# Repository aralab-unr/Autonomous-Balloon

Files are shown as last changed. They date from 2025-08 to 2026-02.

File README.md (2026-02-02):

<div align="center">
    <h2>Autonomous Balloon: Autonomous Balloon based Adaptive Sliding Mode Control and Infinite-Horizon POMDP</h2>
</div>

# Highlights
Our paper has been accepted for publication in ICRA 2026. If our repository supports your academic projects, please cite our work. Thank you!
[Balloon_POMDP_ASMC_ICRA.pdf](https://github.com/user-attachments/files/25022309/Balloon_POMDP_ASMC_ICRA.pdf)

This project provides a simulation platform for super-pressure balloons, featuring both a Simulink/MATLAB-based simulation and a quasi-physical model implemented in Gazebo/ROS 2. The experiments are conducted on a real platform weighing 75 grams, which is capable of tracking the desired altitude, estimating wind conditions, and making autonomous decisions.

# Simulations
We present results obtained from both Simulink/MATLAB and Gazebo/ROS 2 simulations, using parameters based on a real balloon to evaluate the effectiveness of the proposed method. The results are divided into two parts: (1) tracking the desired altitude, and (2) an autonomous balloon that estimates wind conditions and makes decisions to maintain a specific position.

# Simulink/Matlab
The diagram of the simulation in MATLAB/Simulink is presented as follows:

<p align="center">
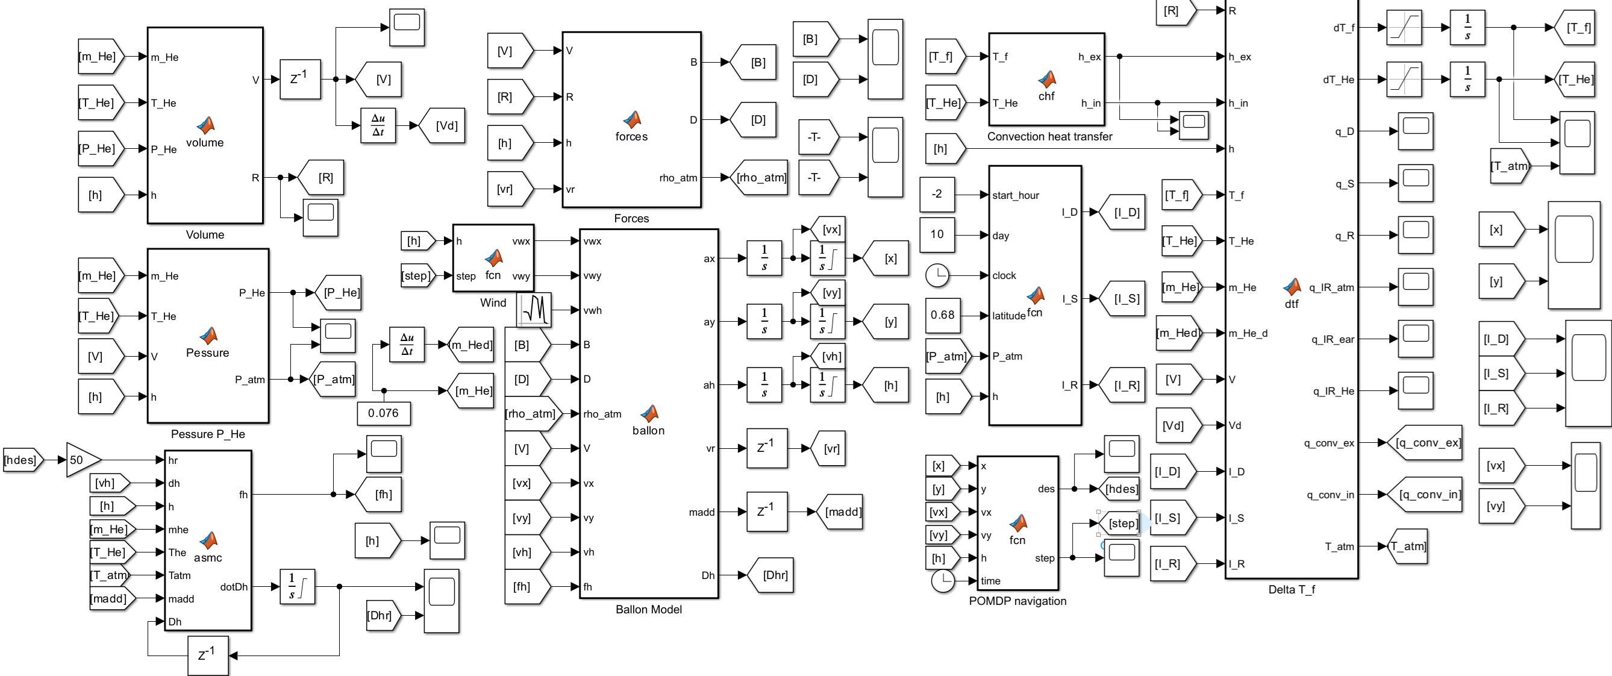
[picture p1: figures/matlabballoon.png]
matlabballoon
  
</p>

The simulation files are located in the BalloonMatlab folder. The SPballoonASMC.slx file is used for tracking the desired altitude, while the SPballoonASMCPOMDPfull.slx file is for simulating the autonomous balloon.

## Gazebo/ROS 2
The visual model of the balloon in Gazebo is shown below:
<p align="center">
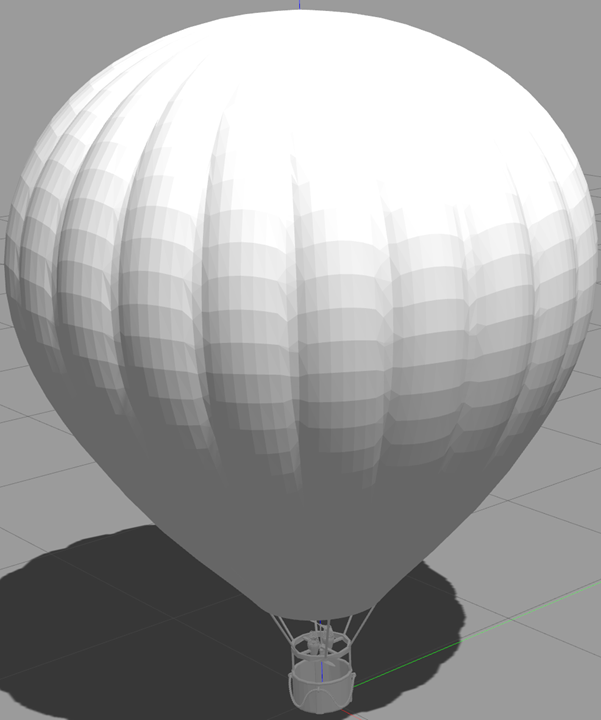
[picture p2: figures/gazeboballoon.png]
gazeboballoon
  
</p>

The simulation on Gazebo/ROS 2 running on the following software setup: 
- Ubuntu 22.04 + ROS2 Humble
- Gazebo 11
- Xarco-ROS-Humble (sudo apt install ros-humble-xacro)
- Gazebo_ros_pkgs (sudo apt install ros-humble-gazebo-ros-pkgs)

To set up the simulation on Gazebo/ROS 2 :

```shell
# Step 1: Create and build a colcon workspace:
$ mkdir -p ~/ros2_ws/src
$ cd ~/ros2_ws/
$ colcon build
$ echo "source ~/ros2_ws/devel/setup.bash" >> ~/.bashrc

# Step 2: Download the source file smcpomdpballoon  on the folder BalloonGazebo into your workspace
$ cd ~/ros2_ws/src

# Step 3: Build the colcon workspace for this package
$ cd ~/ros2_ws
$ colcon build
```

* Note that this project uses a custom plugin. Users need to replace the plugin path in the file /urdf/smcpomdpballoon.urdf.xacro at line 216. Replace: filename="/home/vanchung/dev_ws/install/smcpomdpballoon/lib/smcpomdpballoon/libsmcpomdpballoonplugin.so" with the correct path by changing the username to the name of your computer. Then rebuild the project again to run the simulation.
  
To run the simulation on Gazebo/ROS 2 :

```shell
# Step 1: Run the workspace:
$ ros2 launch smcpomdpballoon model.launch.py

# Step 2: Run the controller for the altitude holding or station keeping
$ ros2 run smcpomdpballoon altitudeholding
$ ros2 run smcpomdpballoon stationkeeping

```

# Experiments
## Design and Hardware Setup
The balloon is designed in SolidWorks, and all parts are 3D-printed. A 36-inch latex balloon is used in the project. The visual design in SolidWorks and the hardware setup are shown in the following figure: 

<p align="center">
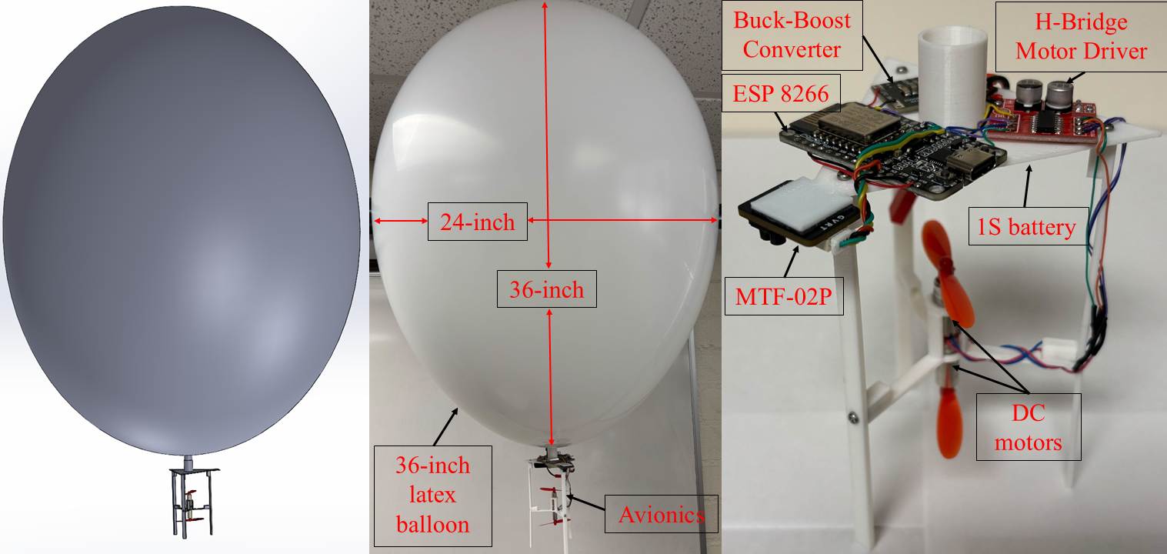
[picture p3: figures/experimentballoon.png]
experimentballoon
  
</p>

The SolidWorks assembly and all the parts used can be found in the Balloon folder. 

The control board is powered by an ESP8266 module, which communicates with the ground station via the TCP protocol. For the indoor prototype, the balloon’s position is measured using the MTF-02P Optical & Range Sensor. All components are carried by a 36-inch latex balloon, with a total system weight of 75 grams. <br> 

For the setup of the station-keeping experiment, refer to the following figure:

<p align="center">
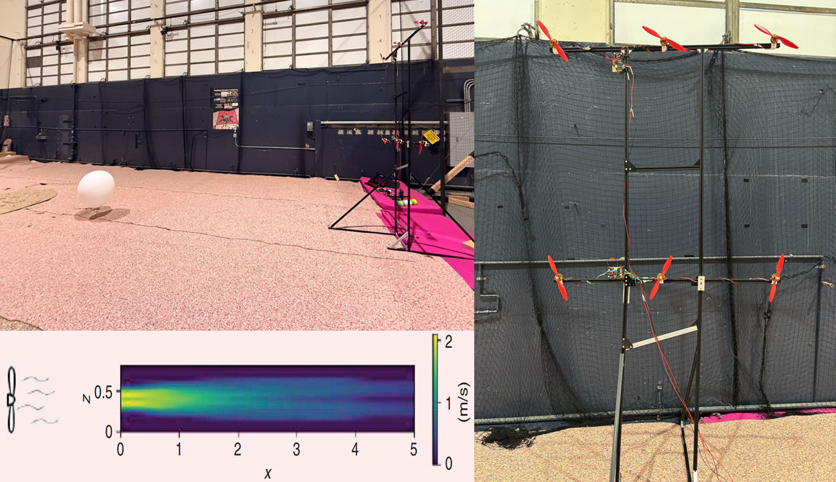
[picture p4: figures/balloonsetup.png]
balloonsetup
  
</p>

## Software Setup
This guide explains how to set up communication between an ESP8266 microcontroller and a ROS2 system using the TCP protocol. The source code is located in the Balloonexperiment folder.

```shell
# Step 1: Create and build a colcon workspace:
$ mkdir -p ~/ros2_ws/src
$ cd ~/ros2_ws/
$ colcon build
$ echo "source ~/ros2_ws/devel/setup.bash" >> ~/.bashrc

# Step 2: Download the source file esp8266server  on the folder Balloonexperiment into your workspace
$ cd ~/ros2_ws/src

# Step 3: Build the colcon workspace for this package
$ cd ~/ros2_ws
$ colcon build
```
To enable communication, the ESP8266 and the PC running ROS2 must be connected to the same Wi-Fi network. Upload the Arduino sketch pomdpballoonesp8266.ino into the ESP 8266, with the corrected IP address of the ROS2 host in line 14. After uploading the code to the ESP8266, run the following command to start the ROS2 TCP server:

```shell
ros2 run esp8266server server
ros2 topic pub /cmdvel std_msgs/msg/Float64MultiArray "data: [1, 0, 0]"
```

# Contact
- [Van Chung Nguyen](mailto:vanchungn@.unr.edu)
- [Hung La](mailto:hla@unr.edu)

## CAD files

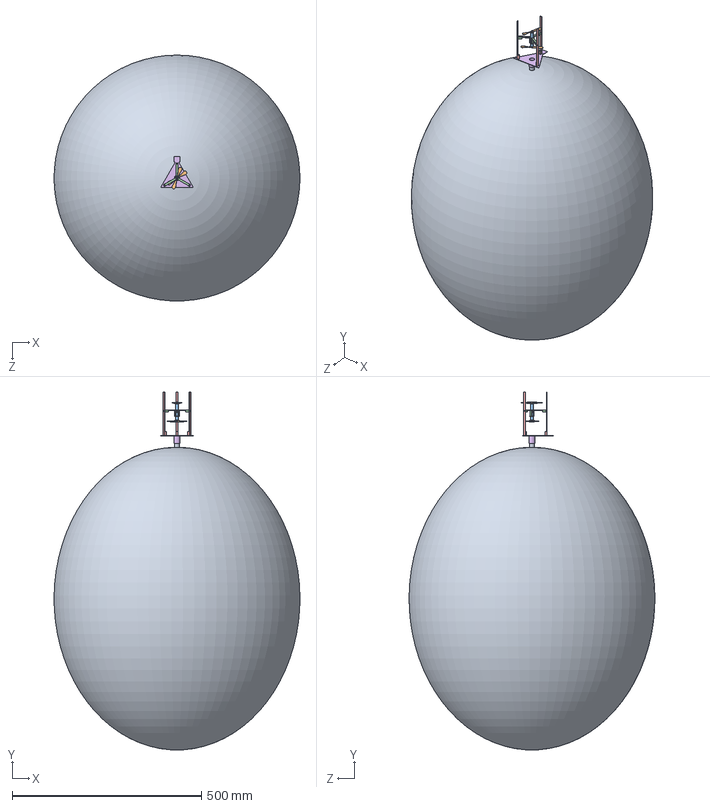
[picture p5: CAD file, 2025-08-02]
Balloon/balloonassemble.SLDASM
649.7 x 946.0 x 649.5 mm
stand
sticknewbase x 3
holdingnew
Coreless DC Motor x 2
propeller x 2
balloon

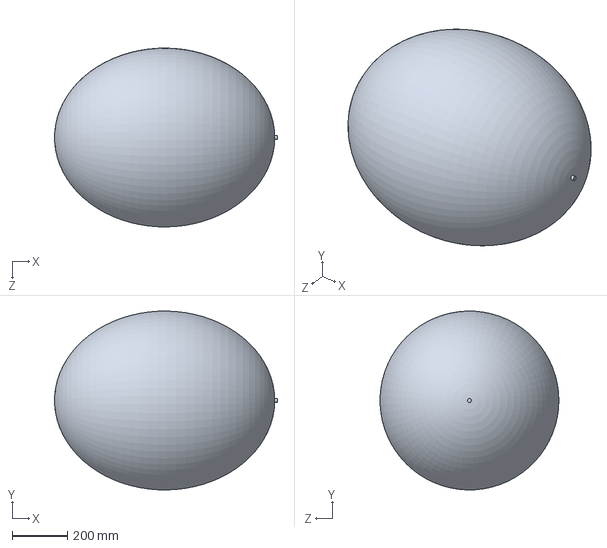
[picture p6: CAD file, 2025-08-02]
Balloon/balloon.SLDPRT
810.0 x 649.7 x 649.5 mm

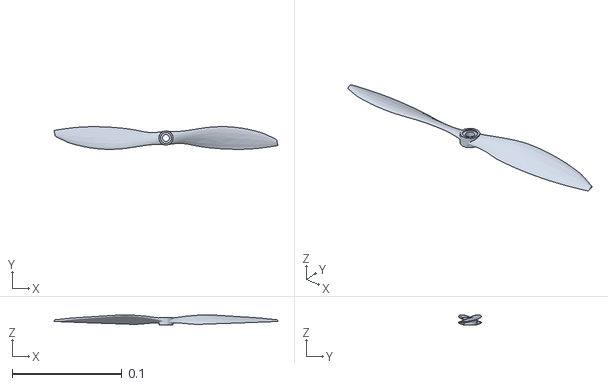
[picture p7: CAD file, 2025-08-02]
BalloonGazebo/smcpomdpballoon/models/propleft.STL
0.204 x 0.0207 x 0.0094

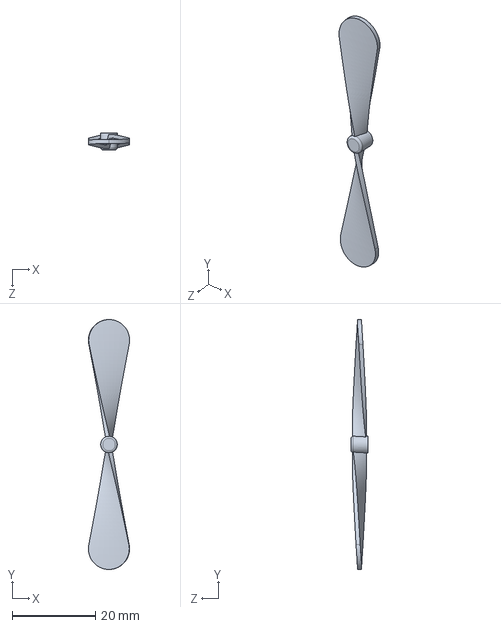
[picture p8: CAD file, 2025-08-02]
Balloon/propeller.SLDPRT
9.89 x 60.0 x 4.00 mm

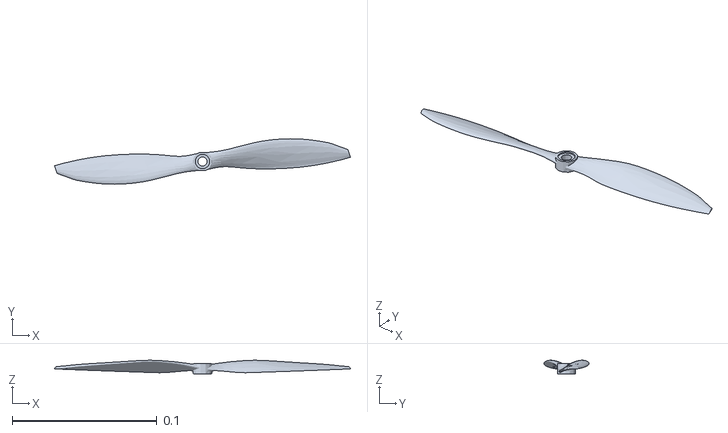
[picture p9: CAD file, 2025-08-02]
BalloonGazebo/smcpomdpballoon/models/propright.STL
0.204 x 0.0314 x 0.0094

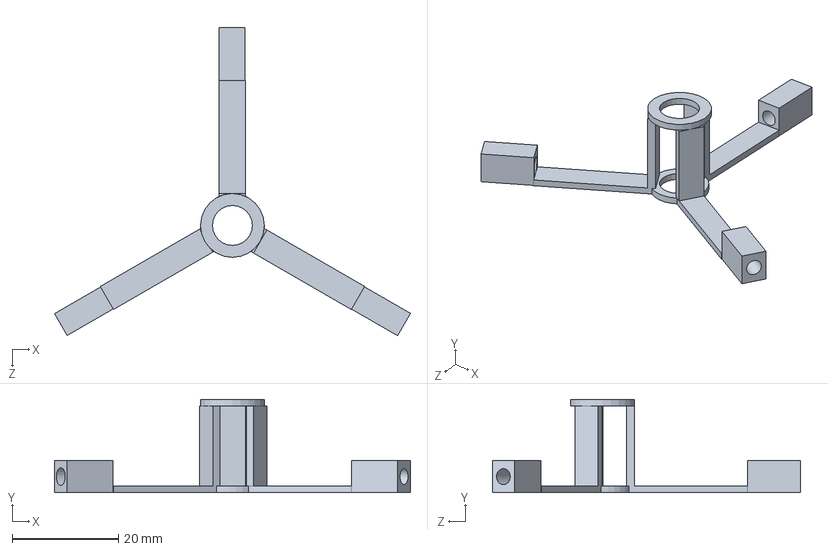
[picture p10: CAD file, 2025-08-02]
Balloon/holdingnew.SLDPRT
66.9 x 17.5 x 58.0 mm

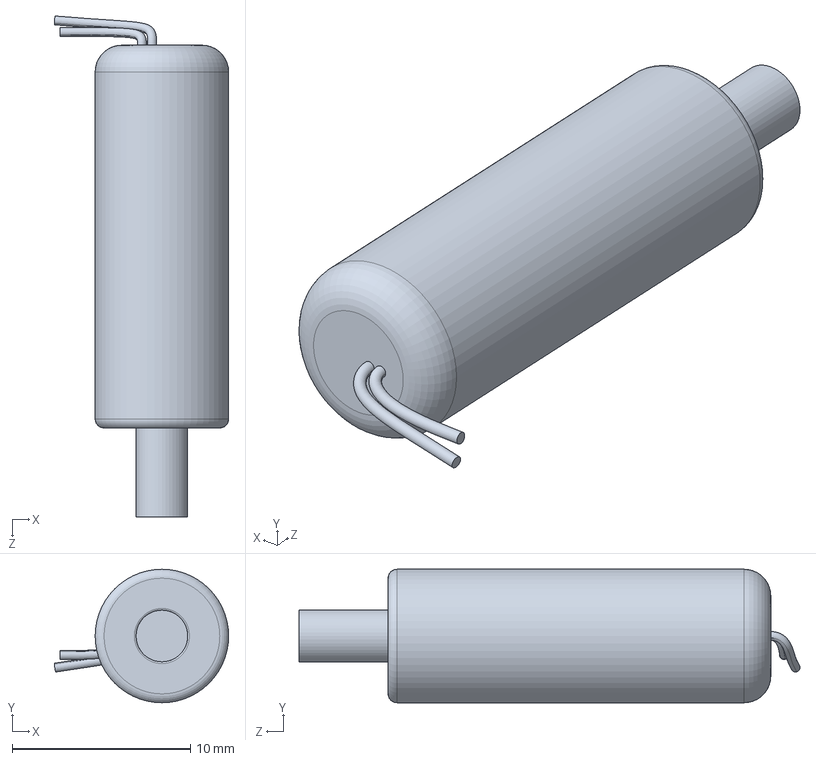
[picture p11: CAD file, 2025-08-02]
Balloon/Coreless DC Motor.SLDPRT
9.79 x 7.50 x 28.1 mm

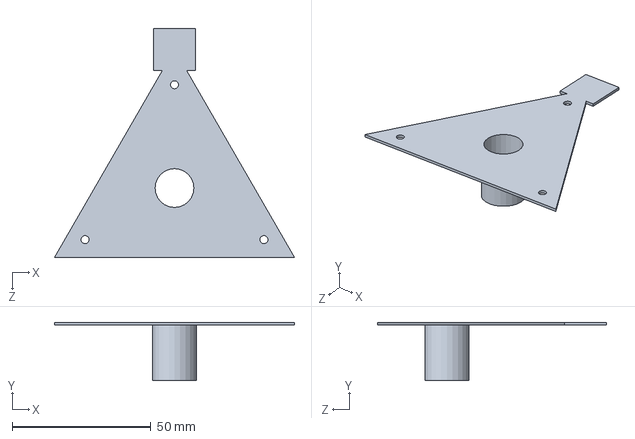
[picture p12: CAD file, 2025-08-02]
Balloon/stand.SLDPRT
86.6 x 21.0 x 82.5 mm

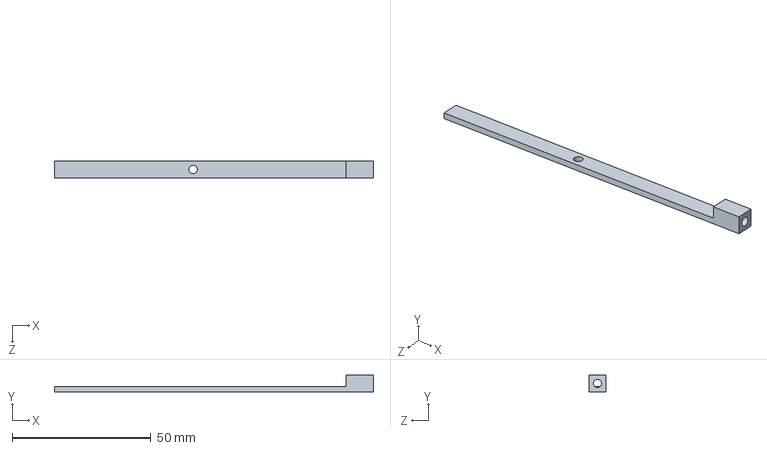
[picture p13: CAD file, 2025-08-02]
Balloon/sticknewbase.SLDPRT
115.0 x 6.00 x 6.00 mm

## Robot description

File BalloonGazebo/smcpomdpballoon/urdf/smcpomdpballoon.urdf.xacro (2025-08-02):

<?xml version="1.0" encoding="utf-8"?>
<robot name="smcpomdpballoon" xmlns:xacro="http://ros.org/wiki/xacro">
  <link name="base_link">
    <inertial>
      <origin xyz="0 0 0" rpy="0 0 0" />
      <mass value="0.52" />
      <inertia ixx="1530000.25" ixy="0" ixz="0" iyy="1530000.25" iyz="0" izz="2075000.5" />
    </inertial>
    <visual>
      <origin xyz="0 0 0" rpy="0 0 0" />
      <geometry>
        <mesh filename="file://$(find smcpomdpballoon)/models/base_link.STL" scale="0.12 0.12 0.12"/>
      </geometry>
      <material name="">
        <color rgba="0.752941176470588 0.752941176470588 0.752941176470588 1" />
      </material>
    </visual>
    <collision>
      <origin xyz="0 0 0.1" rpy="0 0 0" />
      <geometry>
         <box size = "0.25 0.25 0.2" />
      </geometry>
    </collision>
  </link>
  
  <link name="propright">
    <inertial>
      <origin xyz="0 0 0" rpy="0 0 0" />
      <mass value="0.01" />
      <inertia ixx="0.00004" ixy="0" ixz="0" iyy="0.00004" iyz="0" izz="0.000025" />
    </inertial>
    <visual>
      <origin xyz="0 0 0" rpy="0 0 0" />
      <geometry>
        <mesh filename="file://$(find smcpomdpballoon)/models/propright.STL" scale="0.75 0.75 0.75"/>
      </geometry>
      <material name="">
        <color rgba="0.294117647058824 0.294117647058824 0.294117647058824 1" />
      </material>
    </visual>
    <collision>
      <origin xyz="0 0 0" rpy="0 0 0" />
      <geometry>
        <mesh filename="file://$(find smcpomdpballoon)/models/propright.STL" scale="0.75 0.75 0.75"/>
      </geometry>
    </collision>
  </link>
  <joint name="pbr" type="continuous">
    <origin xyz="0 0 0.165" rpy="0 0 0" />
    <parent link="base_link" />
    <child link="propright" />
    <axis xyz="0 0 -1" />
  </joint>

  <link name="propleft">
    <inertial>
      <origin xyz="0 0 0" rpy="0 0 0" />
      <mass value="0.01" />
      <inertia ixx="0.00004" ixy="0" ixz="0" iyy="0.00004" iyz="0" izz="0.000025" />
    </inertial>
    <visual>
      <origin xyz="0 0 0" rpy="0 0 0" />
      <geometry>
        <mesh filename="file://$(find smcpomdpballoon)/models/propleft.STL" scale="0.75 0.75 0.75"/>
      </geometry>
      <material name="">
        <color rgba="0.294117647058824 0.294117647058824 0.294117647058824 1" />
      </material>
    </visual>
    <collision>
      <origin xyz="0 0 0" rpy="0 0 0" />
      <geometry>
        <mesh filename="file://$(find smcpomdpballoon)/models/propleft.STL" scale="0.75 0.75 0.75"/>
      </geometry>
    </collision>
  </link>
  <joint name="pbl" type="continuous">
    <origin xyz="0 0 0.31" rpy="0 0 0" />
    <parent link="base_link" />
    <child link="propleft" />
    <axis xyz="0 0 -1" />
  </joint>

  <link name="propleftbase">
    <inertial>
      <origin xyz="0 0 0" rpy="0 0 0" />
      <mass value="0.01" />
      <inertia ixx="0.00004" ixy="0" ixz="0" iyy="0.00004" iyz="0" izz="0.000025" />
    </inertial>
    <visual>
      <origin xyz="0 0 0" rpy="0 0 0" />
      <geometry>
        <cylinder radius="0.0025" length="0.155" />
      </geometry>
      <material name="">
        <color rgba="0.294117647058824 0.294117647058824 0.294117647058824 1" />
      </material>
    </visual>
    <collision>
      <origin xyz="0 0 0" rpy="0 0 0" />
      <geometry>
        <cylinder radius="0.0025" length="0.155" />
      </geometry>
    </collision>
  </link>

  <joint name="plfbased" type="fixed">
    <origin xyz="0 0 0.2375" rpy="0 0 0" />
    <parent link="base_link" />
    <child link="propleftbase" />
    <axis xyz="0 0 -1" />
  </joint>

  <gazebo>
    <plugin name="gazebo_ros_state" filename="libgazebo_ros_p3d.so">
      <ros>
        <namespace>/droneposition</namespace>
      </ros>
      <update_rate>1000</update_rate> 
      <body_name>base_link</body_name> <!-- Link to track -->
      <frame_name>world</frame_name>
    </plugin>
  </gazebo>

  <gazebo>
  <plugin name="smcpomdpballoonplugin" filename="/home/vanchung/dev_ws/install/smcpomdpballoon/lib/smcpomdpballoon/libsmcpomdpballoonplugin.so">
      <updateRate>1000</updateRate> 
      <publishTf>true</publishTf>
    </plugin>
  </gazebo>

</robot>

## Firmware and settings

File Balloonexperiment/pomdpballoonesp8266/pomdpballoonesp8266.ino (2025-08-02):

#include <ESP8266WiFi.h>
#include <ESP8266HTTPClient.h>
#include <ESP8266WebServer.h>
#include <WiFiClient.h>
#include <SoftwareSerial.h>

#define RX_PIN D7  
#define TX_PIN D8 
SoftwareSerial opticalflowserial(RX_PIN, TX_PIN);

const char* ssid = "NETGEAR80";
const char* password = "grandoboe861";

const char* host = "192.168.1.9"; 
const uint16_t port = 1234;

WiFiClient client;

unsigned long lastSendTime = 0;
int mode = 0;
int direction = 0;
int velocity = 0;

struct State {
  double x, y;
  int z;
};

double epsilon = 0.95;
double epsilon_decay = 0.875;
int episode = 0;
State state = {0, 0, 1};
State prestate = {0, 0, 1};

double belief[5][4];
double prev_belief[5][4];

int actions[3] = {1, -1, 0};
int areaSize[3] = {100, 100, 5};
int goalState[2] = {0, 0};

int hdes = 1.0;

double zr = 0.09;
double arrival_time = -1;
bool is_at_hdes = false;
int actionIdx;
double time_now = 0.0;

const int possibleWinds[4][2] = {
  {-1, -1}, {-1, 1}, {1, -1}, {1, 1}
};

uint32_t LoopTimer;
float dt = 0.01;

float x = 0, y = 0, z = 0;
float xd = 0, yd = 0, zd = 0;

const float Ratm = 287.0;
const float Kssmc = 0.075;
const float Ksmc = 0.125;
const float m = 0.080;
const float g = 9.80;
const float RHe = 2077.0;
const float mhe = 0.0085;
const  float The = 298.0;
const float Tatm = 298.0;
const float madd = 0.04;

const float lambda = 2.25;
const float gamma_val = 0.075;
const float epsat = 0.1;

float fz = 0.0;
float dotDz = 0.0;
float Dz = 0.0;

float dtOptical = 0.02;

const int IN1 = D1;  
const int IN2 = D2;  
const int IN3 = D5; 
const int IN4 = D6; 
int pw1 = 0, pw2 = 0, pw3 = 0, pw4 = 0; 

#define MICOLINK_MSG_HEAD 0xEF
#define MICOLINK_MAX_PAYLOAD_LEN 64
#define MICOLINK_MAX_LEN (MICOLINK_MAX_PAYLOAD_LEN + 7)

enum {
    MICOLINK_MSG_ID_RANGE_SENSOR = 0x51,
};

typedef struct {
    uint8_t head;
    uint8_t dev_id;
    uint8_t sys_id;
    uint8_t msg_id;
    uint8_t seq;
    uint8_t len;
    uint8_t payload[MICOLINK_MAX_PAYLOAD_LEN];
    uint8_t checksum;

    // internal parsing state
    uint8_t status = 0;
    uint8_t payload_cnt = 0;
} MICOLINK_MSG_t;

#pragma pack(push, 1)
typedef struct {
    uint32_t time_ms;
    uint32_t distance;
    uint8_t strength;
    uint8_t precision;
    uint8_t dis_status;
    uint8_t reserved1;
    int16_t flow_vel_x;
    int16_t flow_vel_y;
    uint8_t flow_quality;
    uint8_t flow_status;
    uint16_t reserved2;
} MICOLINK_PAYLOAD_RANGE_SENSOR_t;
#pragma pack(pop)

void setup() {
  Serial.begin(115200);

  for (int i = 0; i < 5; i++) {
    for (int j = 0; j < 4; j++) {
      belief[i][j] = 1.0 / 4.0;
      prev_belief[i][j] = 1.0 / 4.0;
    }
  }

  WiFi.begin(ssid, password);
  Serial.print("Connecting to WiFi");

  while (WiFi.status() != WL_CONNECTED) {
    delay(500);
    Serial.print(".");
  }

  Serial.println("\nWiFi connected!");
  Serial.print("ESP8266 IP: ");
  Serial.println(WiFi.localIP());

  opticalflowserial.begin(115200);

  while (!client.connect(host, port)) {
    Serial.println("Connecting to server...");
    delay(1000);
  }
  Serial.println("Connected to server");

  pinMode(IN1, OUTPUT);
  pinMode(IN2, OUTPUT);
  pinMode(IN3, OUTPUT);
  pinMode(IN4, OUTPUT);

  LoopTimer = micros();
}

void loop() {

  getoptical();
  if (millis() - lastSendTime >= 200) {  
    lastSendTime = millis();
    String payload = "x =" + String(x, 2) + ", y =" + String(y, 2) + ", z =" + String(z, 2) + ", fz =" + String(fz, 2) + ", Dz =" + String(Dz, 2) + ", zr =" + String(zr, 2) + ", actionIdx =" + String(actionIdx) + ", epsilon =" + String(epsilon, 3);
    payload += ", belief=";
    for (int i = 0; i < 5; ++i) {
      for (int j = 0; j < 4; ++j) {
        payload += String(belief[i][j], 2);
        if (i != 4 || j != 3) payload += ","; 
      }
    }
    payload += "\n";

    client.print(payload);

    while (client.available()) {
      String cmd = client.readStringUntil('\n');
      cmd.trim();  
      Serial.print("Received command: ");
      Serial.println(cmd);

      // Split the input string into 3 parts: mode, direction, velocity
      int firstComma = cmd.indexOf(',');
      int secondComma = cmd.indexOf(',', firstComma + 1);

      if (firstComma > 0 && secondComma > firstComma) {
        String modeStr = cmd.substring(0, firstComma);
        String directionStr = cmd.substring(firstComma + 1, secondComma);
        String velocityStr = cmd.substring(secondComma + 1);

        int equalIndexMode = modeStr.indexOf('=');
        int equalIndexDir = directionStr.indexOf('=');
        int equalIndexVel = velocityStr.indexOf('=');

        if (equalIndexMode > 0 && equalIndexDir > 0 && equalIndexVel > 0) {
          mode = modeStr.substring(equalIndexMode + 1).toInt();
          direction = directionStr.substring(equalIndexDir + 1).toInt();
          velocity = velocityStr.substring(equalIndexVel + 1).toInt();
        } else {
          Serial.println("Error: '=' not found in one of the fields.");
        }
      } else {
        Serial.println("Invalid format. Expected: mode=INT,direction=INT,velocity=INT");
      }
    }
  }
  if (mode == 0 & direction == 0) {
    Dz = 0;
    pw1 = velocity;
    pw2 = 0;
    pw3 = 0;
    pw4 = velocity;
  }
  else if (mode == 0 & direction == 1) {
    Dz = 0;
    pw1 = 0;
    pw2 = velocity;
    pw3 = velocity;
    pw4 = 0;
  }
  else if (mode == 1) {
    time_now = millis() / 1000.0;
    double h = z;
    double vh = zd;
    int current_z = constrain((int)(h / 0.4), 1, areaSize[2]);
    double current_pos[3] = {
      constrain(x, -areaSize[0], areaSize[0]),
      constrain(y, -areaSize[1], areaSize[1]),
      (double)current_z
    };
    if (current_z == hdes) {
      if (!is_at_hdes) {
        arrival_time = time_now;
        is_at_hdes = true;
      }
      if ((time_now - arrival_time) >= 1 && arrival_time > 0) {
        episode++;
        state.x = current_pos[0];
        state.y = current_pos[1];
        state.z = current_pos[2];

        updateBelief(prestate.x, prestate.y, state.x, state.y, prestate.z);
        epsilon = max(epsilon * epsilon_decay, 0.001);

        actionIdx = chooseAction(state, belief);
        hdes = state.z + actions[actionIdx];
        hdes = constrain(hdes, 1, areaSize[2]);

        double max_belief_change = 0;
        for (int i = 0; i < 5; i++) {
          for (int j = 0; j < 4; j++) {
            double diff = fabs(belief[i][j] - prev_belief[i][j]);
            if (diff > max_belief_change) max_belief_change = diff;
          }
        }
        if (max_belief_change > 0.25) {
          epsilon = 0.975;
          Serial.print("Belief update threshold crossed: ");
          Serial.println(max_belief_change, 2);
        }

        arrival_time = -1;
        is_at_hdes = false;
        memcpy(prev_belief, belief, sizeof(belief));
        prestate = state;
      }
    } else {
      arrival_time = -1;
      is_at_hdes = false;
    }
    zr = hdes * 0.4 + 0.15;
    //zr = 0.6;
    float zrd = 0.3 * (zr - z);
    float s = (zd - zrd) + lambda * (z - zr);
    float sat_s;
    if (abs(s) > epsat) {
      sat_s = (s > 0) ? 1.0 : -1.0;
    } else {
      sat_s = s / epsat;
    }
    dotDz = gamma_val * s;
    Dz = Dz + dotDz * dt;
    Dz = constrain(Dz, -0.15, 0.15);
    fz = (-Kssmc * sat_s - Ksmc * s - lambda * (zd - zrd)) * (m + madd) - Dz  - (mhe * RHe * The * g) / (Ratm * Tatm) + m * g;
    fz = constrain(fz, 0.1, 0.25);

    int pw = map((int)(fz * 1000), 0, 250, 0, 255);  // Convert float to int for map()
    pw1 = pw;
    pw2 = 0;
    pw3 = 0;
    pw4 = pw;
    
  }
  else {
    Dz = 0;
    pw1 = 0;
    pw2 = 0;
    pw3 = 0;
    pw4 = 0;
  }
  analogWrite(IN1, pw1);
  analogWrite(IN2, pw2);
  analogWrite(IN3, pw3);
  analogWrite(IN4, pw4);
  
  while (micros() - LoopTimer < 10000);
  dt = (micros() - LoopTimer) / 1000000.0;
  LoopTimer = micros();
}

void normalizeBeliefRow(double* row, int len) {
  double sum = 0;
  for (int i = 0; i < len; i++) sum += row[i];
  if (sum > 0) {
    for (int i = 0; i < len; i++) row[i] /= sum;
  }
}

void updateBelief(double prex, double prey, double currentx, double currenty, int z_level) {
  const double alpha = 0.5;
  int z_idx = constrain(z_level - 1, 0, 4);

  double vx = currentx - prex;
  double vy = currenty - prey;

  int w_obs[2] = {0, 0};
  if (fabs(vx) >= 0.1) w_obs[0] = (vx > 0) ? 1 : -1;
  if (fabs(vy) >= 0.1) w_obs[1] = (vy > 0) ? 1 : -1;

  for (int i = 0; i < 4; i++) {
    if (possibleWinds[i][0] == w_obs[0] && possibleWinds[i][1] == w_obs[1]) {
      belief[z_idx][i] = (1.0 - alpha) * belief[z_idx][i] + alpha;
    } else {
      belief[z_idx][i] *= (1.0 - alpha);
    }
  }

  normalizeBeliefRow(belief[z_idx], 4);
}


int chooseAction(State s, double belief[5][4]) {
  if (random(1000) / 1000.0 < epsilon) {
    return random(3);  
  }

  int z_idx = constrain(s.z - 1, 0, 4);
  double best_value = -1;
  int best_idx = 0;
  for (int i = 0; i < 4; i++) {
    if (belief[z_idx][i] > best_value) {
      best_value = belief[z_idx][i];
      best_idx = i;
    }
  }
  return best_idx % 3;  
}

void getoptical() {
  while (opticalflowserial.available()) {
    uint8_t sensor_data = opticalflowserial.read();
    micolink_decode(sensor_data);
  }
}

void micolink_decode(uint8_t data) {
  static MICOLINK_MSG_t msg;

  if (!micolink_parse_char(&msg, data)) return;

  if (msg.msg_id == MICOLINK_MSG_ID_RANGE_SENSOR) {
    MICOLINK_PAYLOAD_RANGE_SENSOR_t payload;
    memcpy(&payload, msg.payload, msg.len);
    dtOptical = 0.02;
    if (payload.distance < 8000 && fabs(payload.flow_vel_x) < 1500 && fabs(payload.flow_vel_y) < 1500) {
      if (dtOptical > 0.0) {
        zd = (payload.distance / 1000.0 - z) / dtOptical;
        z = payload.distance / 1000.0;

        xd = payload.flow_vel_x * z * 0.01;
        yd = payload.flow_vel_y * z * 0.01;

        x = x + xd * dtOptical;
        y = y + yd * dtOptical;
      }
    }
  }
}

bool micolink_parse_char(MICOLINK_MSG_t* msg, uint8_t data) {
  switch (msg->status) {
    case 0:
      if (data == MICOLINK_MSG_HEAD) {
        msg->head = data;
        msg->status = 1;
      }
      break;
    case 1: msg->dev_id = data; msg->status = 2; break;
    case 2: msg->sys_id = data; msg->status = 3; break;
    case 3: msg->msg_id = data; msg->status = 4; break;
    case 4: msg->seq = data; msg->status = 5; break;
    case 5:
      msg->len = data;
      if (msg->len == 0) {
        msg->status = 7;
      } else if (msg->len > MICOLINK_MAX_PAYLOAD_LEN) {
        msg->status = 0;
      } else {
        msg->payload_cnt = 0;
        msg->status = 6;
      }
      break;
    case 6:
      msg->payload[msg->payload_cnt++] = data;
      if (msg->payload_cnt == msg->len) {
        msg->status = 7;
      }
      break;
    case 7:
      msg->checksum = data;
      msg->status = 0;
      return true;
    default:
      msg->status = 0;
      msg->payload_cnt = 0;
      break;
  }
  return false;
}
